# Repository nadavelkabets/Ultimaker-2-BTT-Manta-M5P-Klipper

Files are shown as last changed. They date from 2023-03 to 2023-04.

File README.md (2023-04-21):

< ongoing project >
# Ultimaker 2+ BTT Manta M5P Klipper mod 
The Ultimaker 2 has a fantastic mechanical design that keeps up with current coreXY motion systems. The stiff and lightweight gantry is capable of high acceleration figures with little ringing. 

With that said, electronics improved a lot since 2014.
The Ultimaker 8 bit Arduino based controller, running an old version of Merlin, is really outdated.
These days, 64 bit ARM computers running Klipper, connected to fast 32 bit controllers offer input shaping (reduces ringing), pressure advance (tunes for nozzle pressure), wireless connectivity, silent steppers etc.

The Ultimaker mainboard also has several design flaws that cause visible layer banding, inaccurate temperature readings and LED flickering while the bed heater is running. The old controller also uses "bang-bang" to maintain heatbed temperatures (turns on, overshoots, turns off, undershoots, etc...). The new controller allows for precise PID temperature control.

Here you can find the instructions, components, STL files and printer.cfg to convert your Ultimaker 2 to Klipper.
BTT M5P Github: https://github.com/bigtreetech/Manta-M5P

## Parts requirements:
- The Ultimaker Heatbed is rated for 180W (24V, 7.5A). The print head heater is rated for 25W. Peak power during heating will surpass 200W. Average power during printing will probably be around 100W for PLA and 150-200W for ABS. A 350W power supply was chosen.
- The hotend thermistor can be replaced easily but the heatbed thermistor is soldered. The Manta M5P was chosen to allow a MAX31865 SPI amplifier to connect the PT100 heatbed thermistor.
- The POM nut does not require lubrication and should offer a tight fit to prevent backlash.

## Recommended parts (BOM) - Aliexpress
- BIGTREETECH Manta M5P + CB1 (heatsink) + TMC2209
- BIGTREETECH MAX31865 V2.0 PT100 amplifier
- NTC100K thermistor
- Meanwell LRS-350-24 power supply
- FYSETC POM TR8x8 lead screw nut (recommended)
- M3 screw kit with nuts
- Crimp tool for molex, ferrule and insulated terminals

## Installation notes:
- The part cooling fans are rated for 12V and are connected in series, so you should use a 24V jumper on the fan header.
- The PT100 wires should be connected to the middle two pins of the M5 motor header.

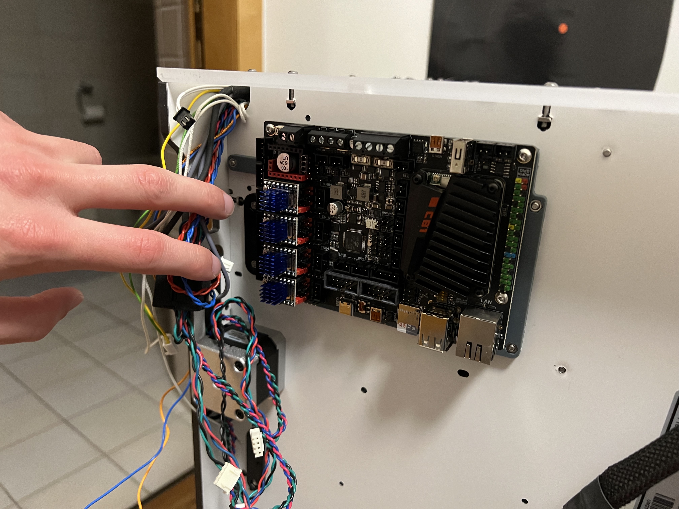
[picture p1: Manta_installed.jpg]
Controller installed with adapter plate


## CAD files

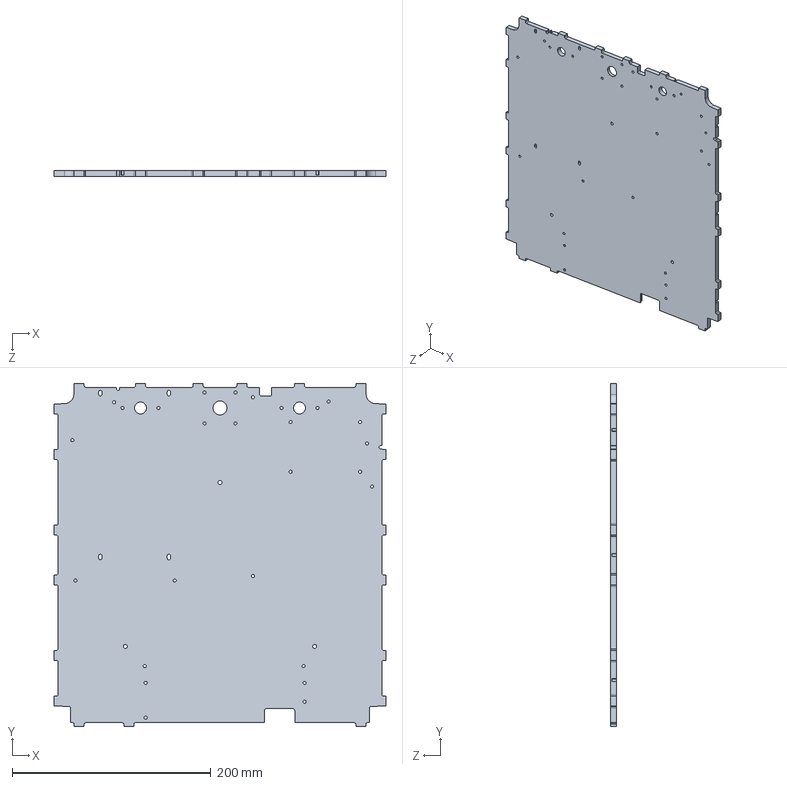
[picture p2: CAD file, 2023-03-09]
Ultimaker2_bottom_plate.STEP
334.2 x 345.6 x 6.00 mm

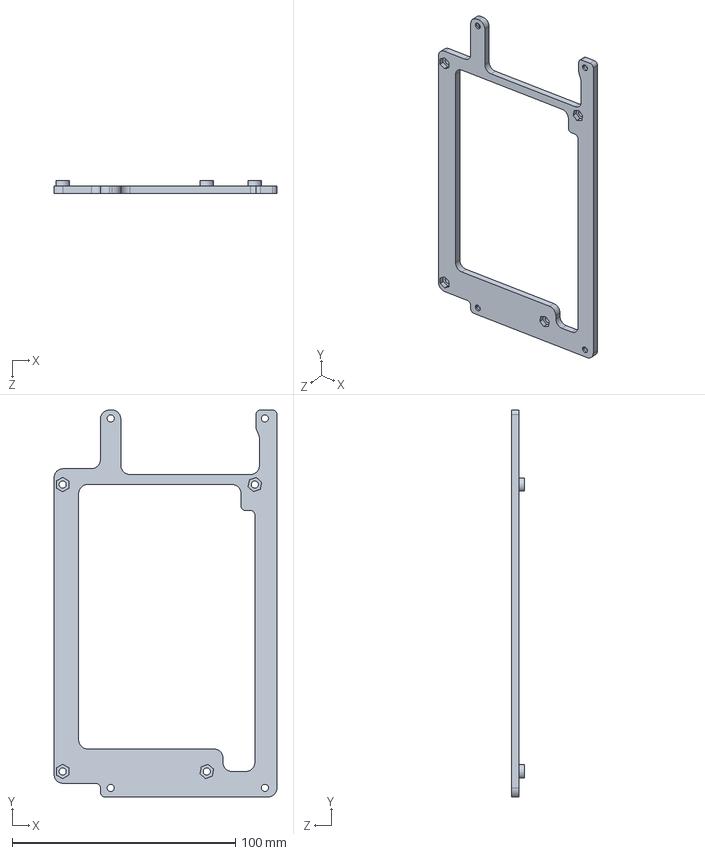
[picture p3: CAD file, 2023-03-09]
UltiManta_adapter.SLDPRT
99.8 x 173.2 x 6.00 mm

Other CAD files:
UltiManta_adapter.STL

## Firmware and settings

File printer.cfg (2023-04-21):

#[include PIS.cfg]
#connect to adxl
[include mainsail.cfg]

# This file contains common pin mappings for the BIGTREETECH Manta M5P
# To use this config, the firmware should be compiled for the
# STM32G0B1 with a "8KiB bootloader" "8 MHz crystal"
# and "USB (on PA11/PA12)" or "CAN bus (on PD0/PD1)".

# See docs/Config_Reference.md for a description of parameters.

#Set location of bed level adjustment screws
[bed_screws]
screw1: 20, 20
screw2: 210, 20
screw3: 110, 180

[input_shaper]
shaper_type_x = ei
shaper_freq_x = 51.2
shaper_type_y = ei
shaper_freq_y = 47.8

#Home Z axis before XY to prevent head collision
[homing_override]
axes: xyz
gcode:
    G28 Z0
    G28 X0 Y0

[stepper_x]
step_pin: PC8
dir_pin: !PC9
enable_pin: !PA15
microsteps: 16
rotation_distance: 40
endstop_pin: !PD3
position_endstop: 0
position_max: 223
homing_speed: 50

[stepper_y]
step_pin: PA10
dir_pin: PA14
enable_pin: !PA13
microsteps: 16
rotation_distance: 40
endstop_pin: !PD2
position_endstop: 223
position_max: 223
homing_speed: 50

[stepper_z]
step_pin: PC6
dir_pin: !PC7
enable_pin: !PA9
microsteps: 16
rotation_distance: 8
endstop_pin: !PC3
#position_endstop: 215
position_max: 215
homing_speed: 15

[extruder]
step_pin: PB12
dir_pin: !PB11
enable_pin: !PA8
microsteps: 16
rotation_distance: 8.67208
nozzle_diameter: 0.400
filament_diameter: 2.850
heater_pin: PA7
sensor_type: Generic 3950
sensor_pin: PA2
control: pid
pid_Kp: 21.527
pid_Ki: 1.063
pid_Kd: 108.982
min_temp: 0
max_temp: 250

#[filament_switch_sensor material_0]
#switch_pin: PC2

#[extruder1]
#step_pin: PB0
#dir_pin: PB1
#enable_pin: !PC4
#heater_pin: PA7
#sensor_pin: PA2
#...

[heater_bed]
heater_pin: PA5
sensor_type: MAX31865
sensor_pin: PA6
spi_software_sclk_pin: PB13
spi_software_miso_pin: PB14
spi_software_mosi_pin: PB15
rtd_nominal_r: 100
rtd_reference_r: 430
rtd_num_of_wires: 2
min_temp: 0
max_temp: 110

[fan]
pin: PA3

[heater_fan fan1]
pin: PA4

#[heater_fan SoC_fan]
#pin: CB1: gpio79
#pin: RPI: gpio26

[mcu]
serial: /dev/serial/by-id/usb-Klipper_stm32g0b1xx_3C001F000C504B5735313920-if00

[printer]
kinematics: cartesian
max_velocity: 100
max_accel: 2000
max_z_velocity: 15
max_z_accel: 50

########################################
# TMC2209 configuration
########################################

[tmc2209 stepper_x]
uart_pin: PD9
run_current: 0.800
diag_pin: PD3
stealthchop_threshold: 999999

[tmc2209 stepper_y]
uart_pin: PD8
run_current: 0.800
diag_pin: PD2
stealthchop_threshold: 999999

[tmc2209 stepper_z]
uart_pin: PB10
run_current: 0.800
diag_pin: PC3
stealthchop_threshold: 999999

[tmc2209 extruder]
uart_pin: PB2
run_current: 0.600
diag_pin: PC2
stealthchop_threshold: 999999


[board_pins]
aliases:
    # EXP1 header
    EXP1_1=PD5, EXP1_3=PB3, EXP1_5=PB5, EXP1_7=PB7, EXP1_9=<GND>,
    EXP1_2=PD4,  EXP1_4=PD6, EXP1_6=PB4, EXP1_8=PB6, EXP1_10=<5V>,
    # EXP2 header
    EXP2_1=PB14, EXP2_3=PB8, EXP2_5=PC10, EXP2_7=PC12,  EXP2_9=<GND>,
    EXP2_2=PB13, EXP2_4=PB9, EXP2_6=PB15, EXP2_8=<RST>, EXP2_10=<NC>

# See the sample-lcd.cfg file for definitions of common LCD displays.

#[bltouch]
#sensor_pin: PC13
#control_pin: PC15

# Proximity switch
#[probe]
#pin: PC15

#[neopixel my_neopixel1]
#pin: PC11

#[neopixel my_neopixel2]
#pin: PC14

#[adxl345]
#cs_pin: PC0
#spi_bus: spi2

#*# <---------------------- SAVE_CONFIG ---------------------->
#*# DO NOT EDIT THIS BLOCK OR BELOW. The contents are auto-generated.
#*#
#*# [stepper_z]
#*# position_endstop = 211.200
#*#
#*# [heater_bed]
#*# control = pid
#*# pid_kp = 73.590
#*# pid_ki = 1.330
#*# pid_kd = 1018.297
